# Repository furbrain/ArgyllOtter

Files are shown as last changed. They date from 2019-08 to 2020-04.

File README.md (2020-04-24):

# Shetland Attack Pony: Mobile

This is the code, construction files, pcb designs and firmware for the Shetland Attack Pony: Mobile, an 
entry to [Pi Wars 2020](https://piwars.org/).

## Why the silly name?
For the last 10 years, I have been developing a cave surveying tool called the [Shetland Attack Pony](https://github.com/furbrain/SAP5/). This uses a laser range finder, an OLED screen and a 9 axis magnetometer, accelerometer and gyro, and a PIC controller. The robot uses all of these components plus some motors and a raspberry pi, so it seemed a fitting name.

## What parts did you use?
Most of the chassis we have made ourselves with laser-cut acrylic and 3d printed parts. We have made our own pcbs with a CNC engraver/miller. 

Other components used:
* Raspberry Pi 3A
* 2200 mAh LiPo Battery (11.1V)
* [FIT0493](https://www.dfrobot.com/product-1462.html) 12V motor with encoder
* [TLE52602 motor driver](https://uk.rs-online.com/web/p/motor-driver-ics/9062978/) (x4)
* [PIC16F18877](https://www.microchip.com/wwwproducts/en/PIC16F18877) as a motor sub-controller - this allows the PI to
send a command over I2C saying "Drive forward 1m, then stop", this makes some of the autonomous challenges much easier
* [MPU9250](https://shop.pimoroni.com/products/sparkfun-imu-breakout-mpu-9250) 9 axis magnetometer, gyro and accelerometer
* [Laser range finder from aliexpress](https://www.aliexpress.com/item/4000429728611.html)

For the autonomous challenges:
* A caving helmet and light!
* A Raspberry Pi Zero Camera

For the Zombie Apocalypse Challenge:
* [Atomic power popper](https://www.amazon.co.uk/ATOMIC-POWER-POPPER-Battle-Foams/dp/B07GV3S912) - Cut this down to 
make the barrel of the cannon
* [BMP388](https://shop.pimoroni.com/products/adafruit-bmp388-precision-barometric-pressure-and-altimeter) Pressure sensor
* Another MPU9250 to measure inclination
* 12V air pump to pressurise the barrel.

## What software did you use?

We used [Freecad](https://www.freecadweb.org/) to design all the laser-cut and 3d printed parts, and  we used [gEDA](http://www.geda-project.org/) for all the PCB design.

We also used the following python libraries:
* [OpenCV](https://opencv.org/) for computer vision
* [shapely](https://pypi.org/project/Shapely/) and [pyvisgraph](https://github.com/TaipanRex/pyvisgraph) to work out an efficient route through barrels for Eco-Disaster

For the simulation code we used [pygame](http://pygame.org) for the top downview and [vtk](https://pypi.org/project/vtk/) for the 3d view

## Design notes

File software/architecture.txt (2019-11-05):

Software organisation options

Have separate functions which are called for each mode
    Pros: Simple
    Cons: Changes in controller etc need to be duplicated - violates DRY
    
Have classes for each mode which are polled at frequent intervals
    Pros: Can abstract out controller mechanism
        : Allows manager code to abort if needed
    
    Cons: More complex
          How de we handle the case where we are doing complex CV stuff and over-run
          our time slot? Maybe do the complex stuff in separate slot and poll for completion?
          
Solution:
    Total asynchronous scheme
         use asyncio
         means "main function" can keep an eye on voltage, check for home signals etc
         really quite complex

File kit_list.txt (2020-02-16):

Tools:
    Precision screwdriver kit
    Socket set
    Multimeter
    mosquito pliers
    PIC programmer
    serial connector
    crimper
    picoscope
    Glue gun
    Drill
    Calipers?

General parts:
    M3:
        40mm bolt
        20mm bolt
        nuts
        washers
        insets
        2 x 3mm spacer
        3 x 4mm bearing
        4 x 10mm hex spacer
         
    M5:
        bolt
        nuts
    jumper cables:
        male-female
        male-male
        female-female

    JST EH:
        2,4,6-way housing
        contacts
        
    Electrical tape
    
    Bungee cord
    
Controller
    
Drivetrain
    2 x Rods
    2 x springs
    1 x motor
    1 x cable
    
Grabber
    1 each of each possible part (maybe use old wooden ones)
    Servo horn adapter
    
Shooter
    1 each of support bridges (maybe use old wooden ones)
    
Laser
    1 spare unit

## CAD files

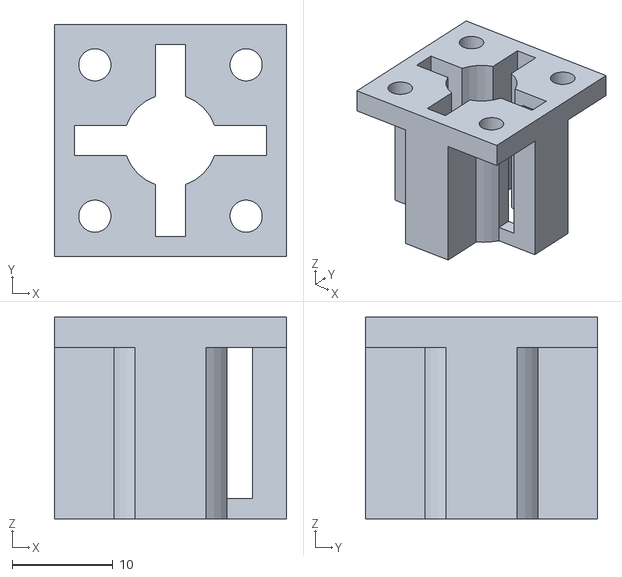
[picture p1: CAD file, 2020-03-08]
challenges/mount.stl
23.0 x 23.0 x 20.0

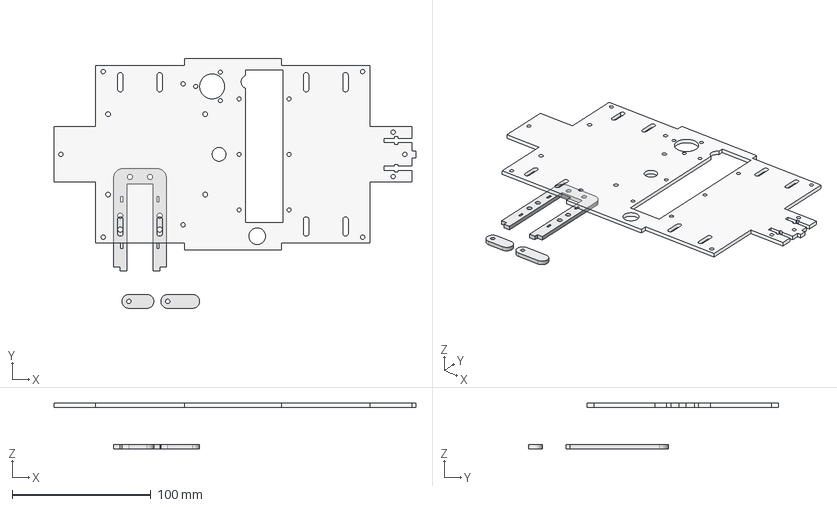
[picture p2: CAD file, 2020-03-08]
drivetrain/base.FCStd
261.0 x 180.0 x 33.0 mm
Leaf
Upper Plane
Lug1
Lug002

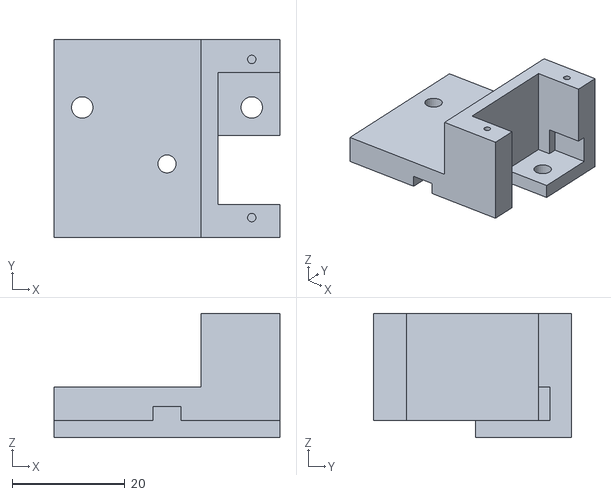
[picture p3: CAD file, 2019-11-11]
grabber/grab_mount.stl
40.0 x 35.0 x 22.0

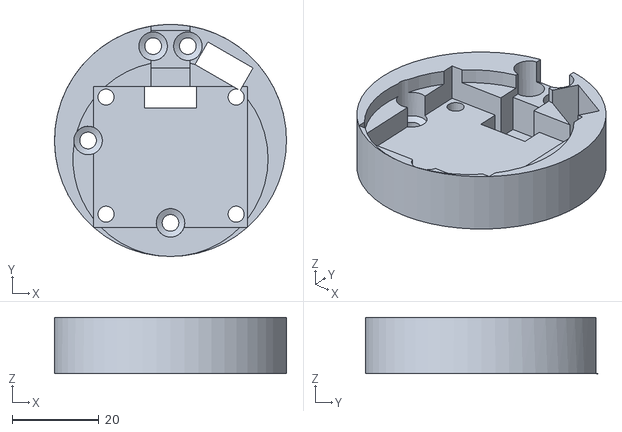
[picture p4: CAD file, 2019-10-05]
interface/headset_top.stl
53.5 x 53.5 x 13.0

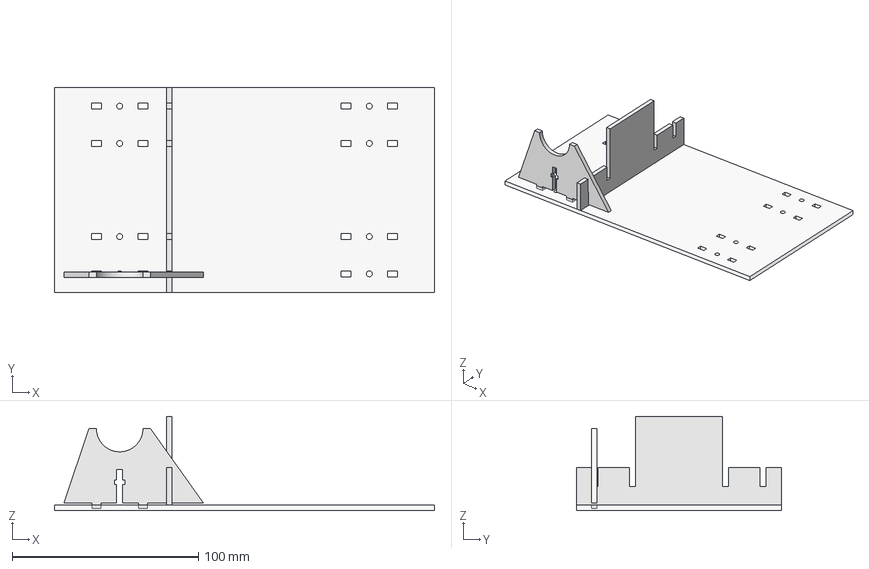
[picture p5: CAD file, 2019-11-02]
mount/mount.FCStd
204.0 x 110.0 x 50.5 mm
Stilt
Base
strut

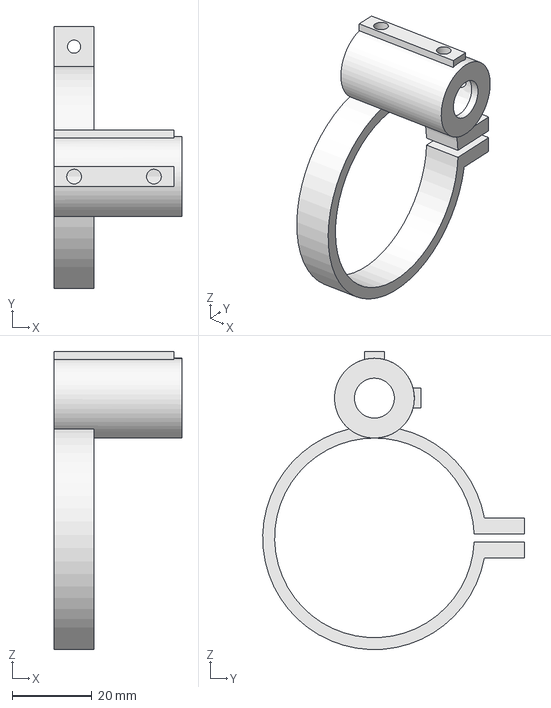
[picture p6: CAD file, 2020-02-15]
shooter/barrel_parts.FCStd
32.0 x 65.5 x 74.7 mm

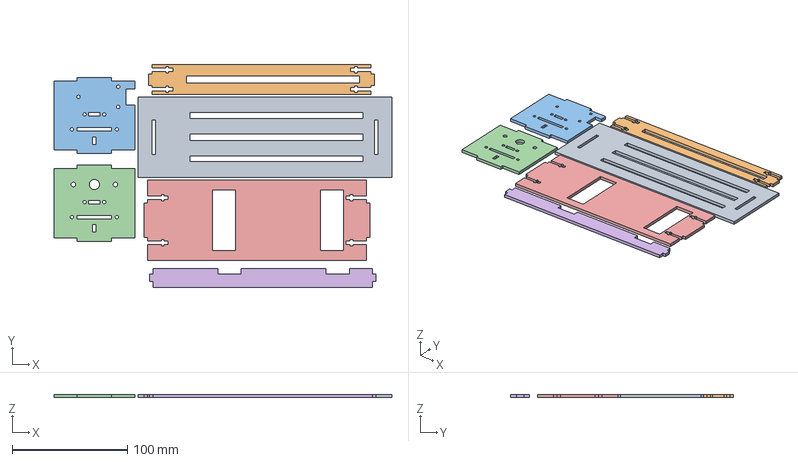
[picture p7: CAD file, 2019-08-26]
snapper/trigger/frame.FCStd
293.0 x 193.2 x 3.00 mm
Top panel
Carriage Support
Front panel
Back panel
Bottom panel
Support panel

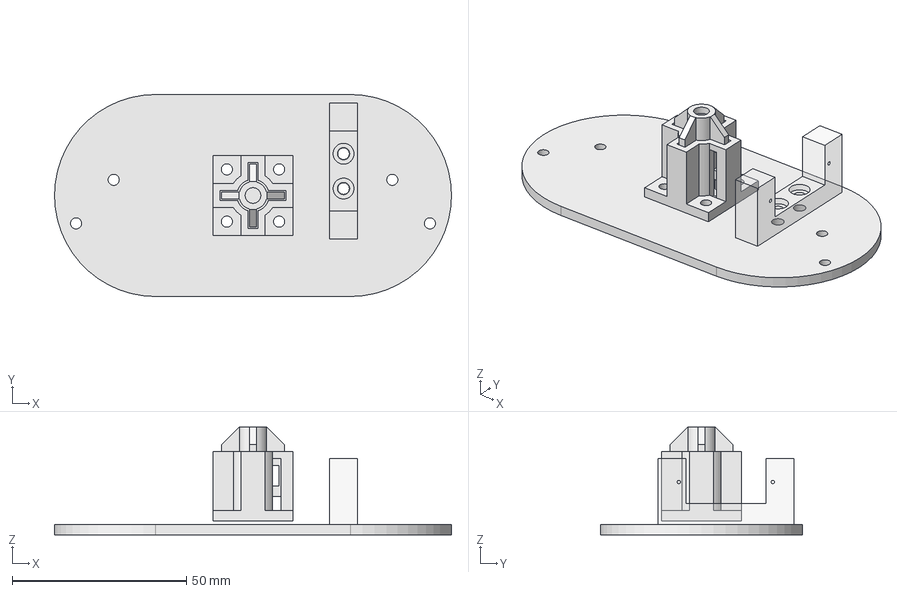
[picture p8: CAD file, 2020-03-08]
challenges/fulcrum3.FCStd
114.0 x 58.0 x 31.0 mm
slider
Mount
base
servo mount

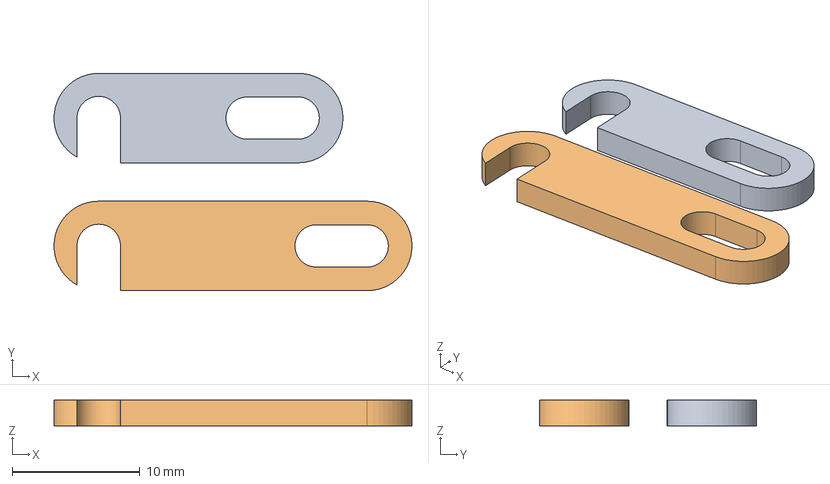
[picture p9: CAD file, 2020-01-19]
drivetrain/clips.FCStd
28.0 x 17.0 x 2.00 mm
A
B

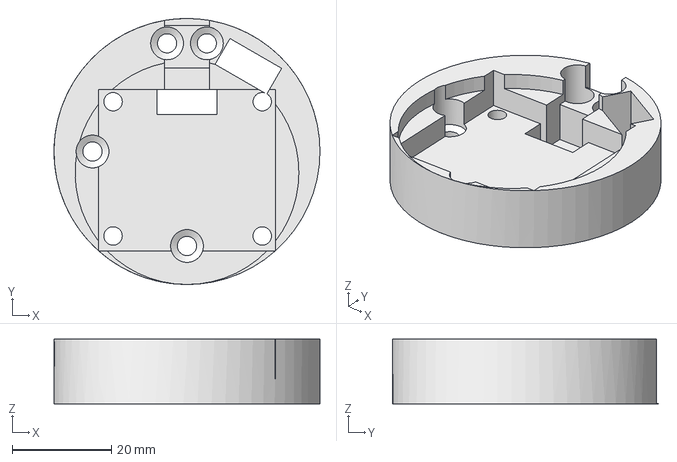
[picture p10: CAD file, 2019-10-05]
interface/headset.FCStd
53.5 x 53.5 x 13.0 mm

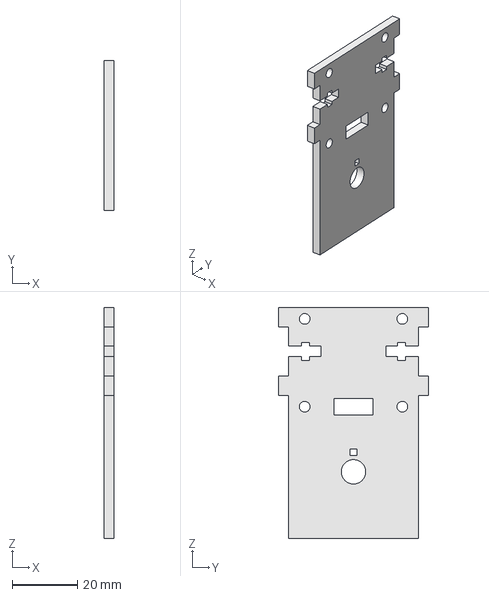
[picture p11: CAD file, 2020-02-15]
shooter/mount.FCStd
3.00 x 46.0 x 71.0 mm

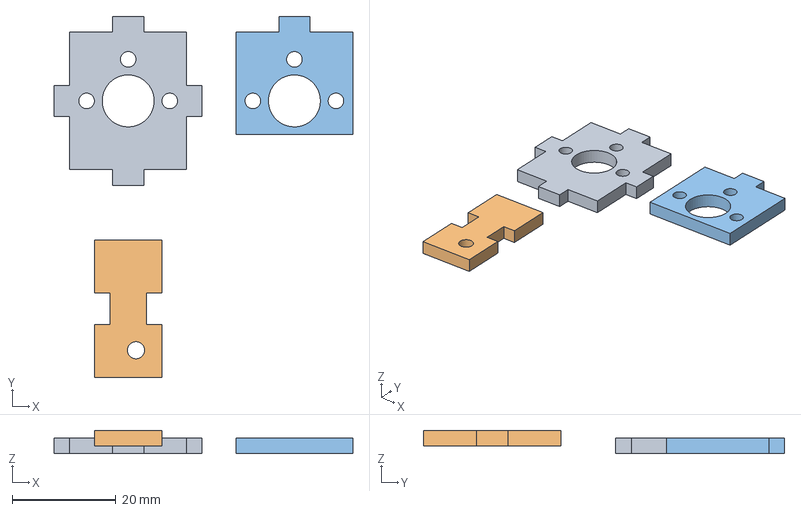
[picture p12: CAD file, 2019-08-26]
snapper/trigger/carriage.FCStd
57.5 x 69.5 x 4.50 mm
Base
SidePanel
Gap

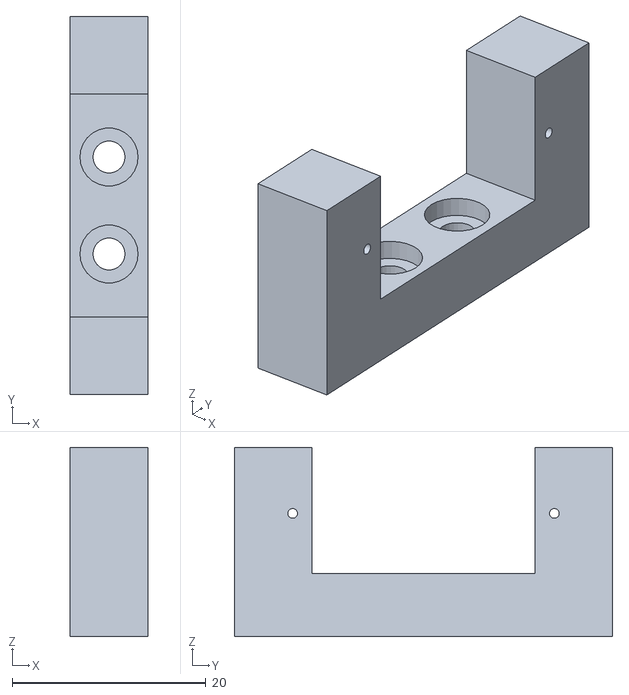
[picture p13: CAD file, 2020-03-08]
challenges/prod_mount.stl
8.00 x 39.0 x 19.5

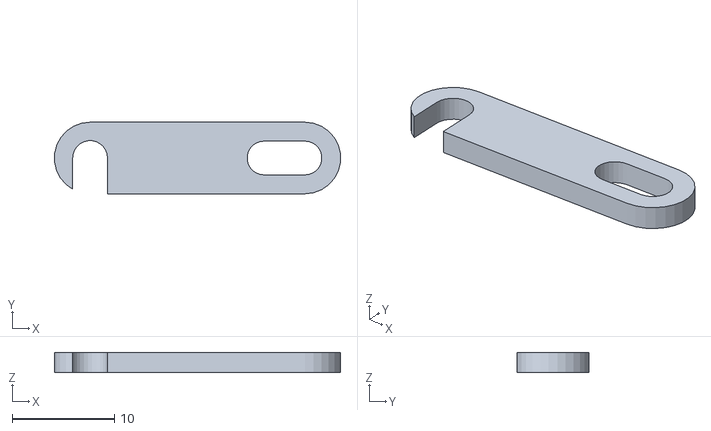
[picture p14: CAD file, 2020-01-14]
drivetrain/clip_b.stl
28.0 x 7.00 x 2.00

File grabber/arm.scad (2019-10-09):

// CSG file generated from FreeCAD 0.18.1.
group() {
 group(){
polyhedron ( points = [[-0.487106,3.465938,0.000000],[-0.487106,3.465938,3.000000],[18.978024,51.643826,0.000000],[18.978024,51.643826,3.000000],[0.487106,-3.465938,0.000000],[0.487106,-3.465938,3.000000],[24.494099,55.953453,0.000000],[24.494099,55.953453,3.000000],[1.850000,-0.000000,0.000000],[28.248360,20.624659,0.000000],[23.586061,53.798641,0.000000],[1.850000,-0.000000,3.000000],[28.248360,20.624659,3.000000],[23.586061,53.798641,3.000000],[-0.487106,3.465938,1.500000],[18.978024,51.643826,1.500000],[7.059635,5.558835,0.000000],[13.807546,9.533658,0.000000],[19.296766,15.119530,0.000000],[23.153217,21.935783,0.000000],[25.114086,29.517900,0.000000],[25.045744,37.349174,0.000000],[22.952847,44.895916,0.000000],[7.059635,5.558835,3.000000],[13.807546,9.533658,3.000000],[19.296766,15.119530,3.000000],[23.153217,21.935783,3.000000],[25.114086,29.517900,3.000000],[25.045744,37.349174,3.000000],[22.952847,44.895916,3.000000],[0.487106,-3.465938,1.500000],[-3.245143,1.311123,0.000000],[-2.758038,-2.154815,0.000000],[-3.245143,1.311123,3.000000],[-2.758038,-2.154815,3.000000],[24.494099,55.953453,1.500000],[21.248955,57.264580,0.000000],[18.490917,55.109764,0.000000],[21.248955,57.264580,3.000000],[18.490917,55.109764,3.000000],[7.992446,-1.594647,0.000000],[14.944714,1.796201,0.000000],[21.040060,6.558408,0.000000],[26.012091,12.483843,0.000000],[29.643503,19.313536,0.000000],[31.775587,26.748999,0.000000],[32.315163,34.465263,0.000000],[31.238644,42.125092,0.000000],[28.593081,49.393711,0.000000],[-0.925000,1.602147,0.000000],[-0.925000,-1.602147,0.000000],[25.473360,22.226807,0.000000],[25.473360,19.022512,0.000000],[20.811062,55.400787,0.000000],[20.811062,52.196491,0.000000],[7.992446,-1.594647,3.000000],[14.944714,1.796201,3.000000],[21.040060,6.558408,3.000000],[26.012091,12.483843,3.000000],[29.643503,19.313536,3.000000],[31.775587,26.748999,3.000000],[32.315163,34.465263,3.000000],[31.238644,42.125092,3.000000],[28.593081,49.393711,3.000000],[-0.925000,-1.602147,3.000000],[-0.925000,1.602147,3.000000],[25.473360,19.022512,3.000000],[25.473360,22.226807,3.000000],[20.811062,52.196491,3.000000],[20.811062,55.400787,3.000000],[1.850000,-0.000000,1.500000],[28.248360,20.624659,1.500000],[23.586061,53.798641,1.500000],[21.326979,48.159222,0.160588],[24.953423,37.960323,0.160588],[24.724274,27.138304,0.160588],[20.669365,17.102055,0.160588],[13.316594,9.158165,0.160588],[3.623200,4.340831,0.160588],[25.330978,32.538895,0.160588],[23.603994,43.224686,0.160588],[17.354227,12.795743,0.160588],[8.688965,6.308692,0.160588],[23.153217,21.935783,0.160588],[-2.693777,2.234628,0.758522],[-1.973478,-2.890568,0.758522],[-3.465938,-0.487106,0.758522],[22.324417,57.248833,0.758522],[18.246017,54.062439,0.758522],[19.581245,56.556679,0.758522],[30.102057,44.484524,0.000000],[6.751485,4.040147,0.000000],[2.859724,-2.700582,0.000000],[26.210295,51.225250,0.000000],[14.535009,4.040147,0.000000],[18.426771,10.780876,0.000000],[22.318533,17.521606,0.000000],[26.210295,24.262335,0.000000],[30.102057,31.003063,0.000000],[26.210295,37.743793,0.000000],[30.102057,44.484524,3.000000],[6.751485,4.040147,3.000000],[2.859724,-2.700582,3.000000],[26.210295,51.225250,3.000000],[14.535009,4.040147,3.000000],[18.426771,10.780876,3.000000],[22.318533,17.521606,3.000000],[26.210295,24.262335,3.000000],[30.102057,31.003063,3.000000],[26.210295,37.743793,3.000000],[0.138191,1.844831,0.668289],[0.138191,-1.844831,0.668289],[-1.850000,-0.000000,0.668289],[26.536551,22.469490,0.668289],[26.536551,18.779827,0.668289],[24.548361,20.624659,0.668289],[21.874252,55.643471,0.668289],[21.874252,51.953808,0.668289],[19.886061,53.798641,0.668289]], triangles = [[73,15,2],[22,73,2],[15,73,3],[20,79,21],[75,27,20],[19,75,20],[28,29,80],[74,21,28],[21,79,28],[79,20,27],[28,79,27],[80,74,28],[73,22,29],[3,73,29],[80,29,22],[80,22,21],[21,74,80],[81,25,18],[17,81,18],[77,24,17],[26,76,25],[25,81,24],[17,24,81],[76,18,25],[78,0,14],[14,1,78],[23,78,1],[24,77,82],[82,16,23],[82,23,24],[17,16,82],[82,77,17],[78,23,16],[0,78,16],[75,83,26],[26,27,75],[83,76,26],[76,83,19],[19,18,76],[83,75,19],[32,4,85],[30,34,85],[85,34,32],[34,30,5],[4,30,85],[14,0,84],[34,33,86],[14,33,1],[33,14,84],[86,33,31],[0,31,84],[86,32,34],[31,32,86],[84,31,33],[37,2,88],[15,39,88],[88,39,37],[39,15,3],[2,15,88],[39,38,89],[87,35,6],[35,38,7],[38,35,87],[89,38,36],[6,36,87],[89,37,39],[36,37,89],[87,36,38],[2,54,22],[10,53,6],[93,22,54],[2,37,54],[93,54,10],[90,99,22],[93,48,22],[47,90,48],[90,22,48],[48,93,6],[93,10,6],[53,36,6],[53,54,37],[37,36,53],[92,8,40],[94,41,91],[4,92,40],[91,40,8],[0,8,49],[92,4,8],[0,91,8],[0,49,31],[32,50,4],[50,8,4],[49,50,31],[32,31,50],[40,91,41],[18,43,95],[41,94,42],[96,52,43],[42,95,43],[19,96,18],[96,43,18],[91,0,16],[18,95,17],[91,16,94],[95,42,94],[95,94,17],[94,16,17],[44,9,45],[43,52,44],[98,45,20],[97,19,20],[97,20,45],[99,98,21],[22,99,21],[20,21,98],[46,99,47],[99,90,47],[45,98,46],[98,99,46],[97,45,9],[51,52,19],[96,19,52],[9,44,52],[51,97,9],[97,51,19],[3,29,68],[13,7,69],[103,68,29],[3,68,39],[103,13,68],[100,29,109],[103,29,63],[62,63,100],[100,63,29],[63,7,103],[103,7,13],[69,7,38],[69,39,68],[39,69,38],[102,55,11],[104,101,56],[5,55,102],[101,11,55],[1,65,11],[102,11,5],[1,11,101],[1,33,65],[34,5,64],[64,5,11],[65,33,64],[34,64,33],[55,56,101],[25,105,58],[56,57,104],[106,58,66],[57,58,105],[26,25,106],[106,25,58],[101,23,1],[25,24,105],[101,104,23],[105,104,57],[105,24,104],[104,24,23],[59,60,12],[58,59,66],[108,27,60],[107,27,26],[107,60,27],[109,28,108],[29,28,109],[27,108,28],[61,62,109],[109,62,100],[60,61,108],[108,61,109],[107,12,60],[67,26,66],[106,66,26],[12,66,59],[67,12,107],[107,26,67],[48,35,63],[48,6,35],[63,35,7],[46,60,45],[44,45,60],[47,61,46],[60,46,61],[61,47,62],[63,47,48],[47,63,62],[43,44,58],[42,58,57],[56,42,57],[58,42,43],[41,55,40],[30,55,5],[30,40,55],[4,40,30],[55,41,56],[42,56,41],[58,44,59],[44,60,59],[50,111,8],[70,111,64],[111,50,64],[64,11,70],[8,111,70],[70,110,8],[64,112,65],[70,11,65],[65,110,70],[112,49,65],[8,110,49],[112,64,50],[49,112,50],[110,65,49],[52,114,9],[71,114,66],[114,52,66],[66,12,71],[9,114,71],[71,113,9],[66,115,67],[71,12,67],[67,113,71],[115,51,67],[9,113,51],[115,66,52],[51,115,52],[113,67,51],[54,117,10],[72,117,68],[117,54,68],[68,13,72],[10,117,72],[72,116,10],[68,118,69],[72,13,69],[69,116,72],[118,53,69],[10,116,53],[118,68,54],[53,118,54],[116,69,53]]);
}
}

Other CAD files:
grabber/mount.FCStd
grabber/arm.FCStd
interface/encoder_adapter.FCStd
shooter/sight2.stl
challenges/Barrel1.stl
challenges/card_holder.FCStd
challenges/card_holder.stl
challenges/fulcrum2.FCStd
challenges/prodder.stl
challenges/prodder2.stl
challenges/slider.stl
drivetrain/Spring mount.FCStd
drivetrain/clip_a.stl
drivetrain/clips.stl
drivetrain/hub.FCStd
drivetrain/hub.stl
drivetrain/laser holder.FCStd
drivetrain/laser_holder.stl
drivetrain/mounts.stl
drivetrain/pcb mounts.FCStd
drivetrain/spring_mount.stl
drivetrain/suspension_lug.FCStd
drivetrain/suspension_lug.stl
grabber/arm.stl
grabber/grab_servo.stl
interface/encoder_adapter.stl
interface/front_panel.FCStd
interface/front_panel.stl
interface/headset.stl
interface/knob.FCStd
interface/knob.stl
shooter/end_cap.stl
shooter/pivoteer.stl
shooter/ring.stl
shooter/servo_adapter.stl
shooter/sight.stl
snapper/trigger/carriage.dxf
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

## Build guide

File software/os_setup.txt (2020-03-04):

System set up notes:
Needs approxeng.input as per lorraine's blog
Need to install servoblaster, this needs to be set as PCM to avoid interfering
with neopixels.
Set to 1us output resolution, set output 0 only
Need to install jgarffs neopixel python lib - which needs to be installed from source as seems to be using an old version of main lib
Install simple-pid python thingy - needs to be installed from github as not on raspbian currently (not currently used...)
Need opencv, imutils, shapely, pyvisgraph, tqdm, sharedarray from pip3
sudo apt install libgeos-dev

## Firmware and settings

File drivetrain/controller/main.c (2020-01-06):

/**
  Generated Main Source File

  Company:
    Microchip Technology Inc.

  File Name:
    main.c

  Summary:
    This is the main file generated using PIC10 / PIC12 / PIC16 / PIC18 MCUs

  Description:
    This header file provides implementations for driver APIs for all modules selected in the GUI.
    Generation Information :
        Product Revision  :  PIC10 / PIC12 / PIC16 / PIC18 MCUs - 1.77
        Device            :  PIC16F18877
        Driver Version    :  2.00
*/

/*
    (c) 2018 Microchip Technology Inc. and its subsidiaries. 
    
    Subject to your compliance with these terms, you may use Microchip software and any 
    derivatives exclusively with Microchip products. It is your responsibility to comply with third party 
    license terms applicable to your use of third party software (including open source software) that 
    may accompany Microchip software.
    
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
    IN NO EVENT WILL MICROCHIP BE LIABLE FOR ANY INDIRECT, SPECIAL, PUNITIVE, 
    INCIDENTAL OR CONSEQUENTIAL LOSS, DAMAGE, COST OR EXPENSE OF ANY KIND 
    WHATSOEVER RELATED TO THE SOFTWARE, HOWEVER CAUSED, EVEN IF MICROCHIP 
    HAS BEEN ADVISED OF THE POSSIBILITY OR THE DAMAGES ARE FORESEEABLE. TO 
    THE FULLEST EXTENT ALLOWED BY LAW, MICROCHIP'S TOTAL LIABILITY ON ALL 
    CLAIMS IN ANY WAY RELATED TO THIS SOFTWARE WILL NOT EXCEED THE AMOUNT 
    OF FEES, IF ANY, THAT YOU HAVE PAID DIRECTLY TO MICROCHIP FOR THIS 
    SOFTWARE.
*/
#pragma warning disable 520
#include "mcc_generated_files/mcc.h"

/*
                         Main application
 */
#include <stdint.h>
#include <stdbool.h>
#include <string.h>
#include <stdlib.h>
#include "comms.h"
#include "pid.h"
#include "wheels.h"

const uint8_t ADC_CHANNELS[] = {
    FRONT_GROUND, 
    FL_CURRENT, 
    FR_CURRENT,
    REAR_GROUND,
    RL_CURRENT,
    RR_CURRENT, 
    BATT_VOLTAGE,
    channel_DAC1
};

volatile bool tick = false;
volatile command_t cmd;

inline void ADCC_SetChannel(uint8_t channel) {
    ADPCH = channel;
}


void OneHundredHertz(void) {
    tick = true;
}

#define within(a, b, delta) (abs(a-b) < delta)

void set_wheel_differentials(int32_t left, int32_t right, int16_t speed) {
    int32_t left_speed, right_speed;
    if (left == right) {
        left_speed = right_speed = speed;
    } else {
        int32_t max_distance = max(abs(left), abs(right));
        left_speed = abs((left * speed) / max_distance);
        right_speed = abs((right * speed) / max_distance);
    }
    wheel_move_to(&wheels[FRONT_LEFT], left_speed);
    wheel_move_to(&wheels[REAR_LEFT], left_speed);
    wheel_move_to(&wheels[FRONT_RIGHT], right_speed);
    wheel_move_to(&wheels[REAR_RIGHT], right_speed);    
}

void Update(void) {
    static uint8_t count = 0;
    wheel_t* whl;
    count++;
    if (count >= SAMPLE_SKIP) {
        FOR_ALL_WHEELS(whl) {
            wheel_update_velocity(whl);
        }
    }
    if (new_command) {
        cmd = *command;
        raise_alert(ALERT_NOALERT);
        FOR_ALL_WHEELS(whl) {
            whl->stopped=false;
        }
        if (cmd.flags & FLAG_RESET_POS) {
                wheels_reset_position();            
        }
        if (cmd.flags & FLAG_SOFT_START) {
            FOR_ALL_WHEELS(whl) {
                wheel_soft_start(whl);
            }
        }
        switch (cmd.mode) {
            case CMD_STOP:
                FOR_ALL_WHEELS(whl) {
                    wheel_stop(whl);
                }
                break;
            case CMD_DRIVE:
                wheel_set_speed(&wheels[FRONT_LEFT], cmd.left_speed);
                wheel_set_speed(&wheels[REAR_LEFT], cmd.left_speed);
                wheel_set_speed(&wheels[FRONT_RIGHT], cmd.right_speed);
                wheel_set_speed(&wheels[REAR_RIGHT], cmd.right_speed);                
                break;
            case CMD_INDIVIDUAL:
                for(uint8_t i = 0; i< 4; i++) {
                    wheel_set_power(&wheels[i], cmd.motor_speed[i]);
                }
                break;
            case CMD_FAST_DISTANCE:
            case CMD_DISTANCE:
                wheel_set_target_pos(&wheels[FRONT_LEFT], cmd.left_distance);
                wheel_set_target_pos(&wheels[REAR_LEFT], cmd.left_distance);
                wheel_set_target_pos(&wheels[FRONT_RIGHT], cmd.right_distance);
                wheel_set_target_pos(&wheels[REAR_RIGHT], cmd.right_distance);
                set_wheel_differentials(cmd.left_distance, cmd.right_distance, cmd.max_speed);
                break;
        }
        new_command = false;
    }
    if (cmd.mode == CMD_DISTANCE) {
        /* left */
        bool nearby = false;
        bool stopped = false;
        
        FOR_ALL_WHEELS(whl) {
            if (whl->stopped) {
                stopped = true;
                break;
            }
            if (within(whl->target_pos, *whl->pos, 10)) {
                raise_alert(ALERT_DESTINATION);
                stopped = true;
                break;
            } else if (within(whl->target_pos, *whl->pos, 300)){
                nearby = true;
            }
        }
        if (stopped) {
            FOR_ALL_WHEELS(whl) {
                wheel_stop(whl);
                cmd.mode = CMD_STOP;
            }
        } else if (nearby) {
            set_wheel_differentials(cmd.left_distance, cmd.right_distance, cmd.max_speed/4);
        } else {
            set_wheel_differentials(cmd.left_distance, cmd.right_distance, cmd.max_speed);
        }
    } else if (cmd.mode == CMD_FAST_DISTANCE) {
        FOR_ALL_WHEELS(whl) {
            if (!*alert_status) {
                if (abs(*whl->pos) > abs(whl->target_pos)) {
                    raise_alert(ALERT_DESTINATION);
                    break;
                } 
            }
        }
    }
    if (count >= SAMPLE_SKIP) {
        count = 0;
        FOR_ALL_WHEELS(whl) {
            if (cmd.mode != CMD_INDIVIDUAL) {
                wheel_update_power(whl);
            }
        }
        FOR_ALL_WHEELS(whl) {
            //wheel_check_current(whl);
        }
    }
}

void ADCResultReady(void) {
    static uint8_t channel_index = 0;
    static uint16_t ground = 0;
    uint8_t channel = ADC_CHANNELS[channel_index];
    uint16_t result = ADCC_GetConversionResult();
    switch (channel) {
        case FRONT_GROUND:
        case REAR_GROUND:
            ground = result;
            break;            
        case FL_CURRENT:
            current[FRONT_LEFT] = (result - ground) * 50;
            break;
        case FR_CURRENT:
            current[FRONT_RIGHT] = (result - ground) * 50;
            break;
        case RL_CURRENT:
            current[REAR_LEFT] = (result - ground) * 50;
            break;           
        case RR_CURRENT:
            current[REAR_RIGHT] = (result - ground) * 50;
            break;
        case BATT_VOLTAGE:
            *batt_voltage = result * 11 * 2;
            break;
        case channel_DAC1:
            *peripheral_voltage = result * 4 * 2;
            break;
        default:
            break;
    }
    channel_index = (channel_index+1) % sizeof(ADC_CHANNELS);
    channel = ADC_CHANNELS[channel_index];
    ADCC_SetChannel(channel);
}


void main(void)
{
    wheel_t* whl;
    SYSTEM_Initialize();
    comms_init();
    wheels_init();
    FOR_ALL_WHEELS(whl) {
        wheel_stop(whl);
    }
    TMR6_SetInterruptHandler(OneHundredHertz);
    TMR1_StartTimer();
    ADCC_SetADIInterruptHandler(ADCResultReady);
    ADCC_SetChannel(FRONT_GROUND);
    // Enable the Interrupts
    INTERRUPT_GlobalInterruptEnable();
    INTERRUPT_PeripheralInterruptEnable();
    while (1)
    {
        while (!tick) {
            NOP();
        }
        tick = false;
        Update();
    }
}
/**
 End of File
*/

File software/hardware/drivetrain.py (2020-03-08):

#!/usr/bin/env python3
import asyncio
import logging
import math
import struct
import time

# noinspection PyUnresolvedReferences
import gpiozero
import numpy as np
# noinspection PyUnresolvedReferences
import smbus

import settings
from util import logged
from . import orientation

I2C_ADDRESS = 0x33
ALERT_REGISTER = 0x5F
RESET_POSITION = 0x01
SOFT_START = 0x02

DRIVE_CAL_FILE = "/home/pi/drivetrain.npz"


class DriveError(Exception):
    pass


# noinspection PyAttributeOutsideInit,PyAttributeOutsideInit,PyAttributeOutsideInit
class DriveCalibration(settings.Settings):
    def default(self):
        self.spin_k = 0
        self.forward_k = 0
        self.reverse_k = 0


class Drive:
    def __init__(self, bus=None, wheel_diameter=70.0, clicks_per_revolution=374):
        if bus is None:
            self.bus = smbus.SMBus(1)
        else:
            self.bus = bus
        self.cal = DriveCalibration()
        self.clicks_per_mm = clicks_per_revolution / (math.pi * wheel_diameter)
        self.orientation = orientation.Orientation(bus=self.bus)
        self.alert = gpiozero.Button(4)
        self.orientation.calibrate_gyro()
        self.stop(reset_position=True)

    def __str__(self):
        return "Drive instance"

    @staticmethod
    def get_flags(soft_start, reset_position):
        flags = 0
        if soft_start:
            flags |= SOFT_START
        if reset_position:
            flags |= RESET_POSITION
        return flags

    def reset_alert(self):
        self.get_alert()
        self.bus.write_i2c_block_data(I2C_ADDRESS, ALERT_REGISTER, [0])

    def get_alert(self):
        return self.bus.read_i2c_block_data(I2C_ADDRESS, ALERT_REGISTER, 1)[0]

    def mm2c(self, *args):
        return [int(x * self.clicks_per_mm) for x in args]

    def c2mm(self, *args):
        return [int(x / self.clicks_per_mm) for x in args]

    @logged
    def stop(self, reset_position=False):
        flags = self.get_flags(soft_start=False, reset_position=reset_position)
        self.bus.write_i2c_block_data(I2C_ADDRESS, 0x0, [0, flags])

    @logged
    def drive(self, left, right=None, soft_start=False, reset_position=False):
        if right is None:
            right = left
        flags = self.get_flags(soft_start, reset_position)
        args = self.mm2c(left, right) + [soft_start]
        command = struct.pack("<BBhhB", 1, flags, *args)
        self.bus.write_i2c_block_data(I2C_ADDRESS, 0x0, list(command))

    @logged
    def goto(self, max_speed, right, left=None, fast=False, soft_start=False, reset_position=True):
        flags = self.get_flags(soft_start, reset_position)
        if fast:
            cmd = 5
        else:
            cmd = 2
        if left is None:
            left = right
        args = self.mm2c(left, right, max_speed)
        # noinspection SpellCheckingInspection
        command = struct.pack("<BBiih", cmd, flags, *args)
        self.bus.write_i2c_block_data(I2C_ADDRESS, 0x0, list(command))

    @logged
    def set_powers(self, fr, fl, rr, rl, soft_start=False, reset_position=False):
        args = fr, fl, rr, rl
        flags = self.get_flags(soft_start, reset_position)
        # noinspection SpellCheckingInspection
        command = struct.pack("<BBhhhh", 4, flags, *args)
        self.bus.write_i2c_block_data(I2C_ADDRESS, 0x0, list(command))

    @logged
    def get_positions(self):
        for i in range(5):
            data = self.bus.read_i2c_block_data(I2C_ADDRESS, 0x10, 0x10)
            positions = struct.unpack("4i", bytes(data))
            if any(abs(x) > 10000 for x in positions):
                print("bad position, trying again")
                time.sleep(0.02)
                continue
            return self.c2mm(*positions)
        # noinspection PyUnboundLocalVariable
        raise DriveError(
            "Couldn't get reasonable positions, latest readings are" + ', '.join(str(x) for x in positions))

    @logged
    async def a_goto(self, max_speed, right, left=None, fast=False, soft_start=False, reset_position=True,
                     accurate=False):
        self.goto(max_speed, right, left, fast, soft_start, reset_position)
        while True:
            await asyncio.sleep(0.01)
            if not self.alert.is_pressed:
                await asyncio.sleep(0.01)
                if accurate:
                    await asyncio.sleep(0.1)
                return np.mean(self.get_positions())

    @logged
    def get_velocities(self):
        data = self.bus.read_i2c_block_data(I2C_ADDRESS, 0x20, 0x08)
        velocities = struct.unpack("4h", bytes(data))
        return self.c2mm(*velocities)

    @logged
    def get_constants(self):
        data = self.bus.read_i2c_block_data(I2C_ADDRESS, 0x30, 0x10)
        p, i, d, ratio = struct.unpack("4f", bytes(data))
        return {'kP': p, 'kI': i, 'kD': d, 'ratio': ratio}

    @logged
    def get_powers(self):
        powers = [0, 0, 0, 0]
        for i in range(5):
            data = self.bus.read_i2c_block_data(I2C_ADDRESS, 0x20, 0x10)
            powers = struct.unpack("<8h", bytes(data))[4:]
            if any(abs(x) > 1024 for x in powers):
                time.sleep(0.01)
                continue
            return powers
        raise DriveError("Couldn't get reasonable powers, latest readings are" + ', '.join(str(x) for x in powers))

    @logged
    def get_currents(self):
        data = self.bus.read_i2c_block_data(I2C_ADDRESS, 0x40, 0x08)
        currents = struct.unpack("4h", bytes(data))
        return [x / 1000 for x in currents]

    @logged
    def get_voltages(self):
        data = self.bus.read_i2c_block_data(I2C_ADDRESS, 0x50, 0x08)
        peripheral, _, main, _ = struct.unpack("4h", bytes(data))
        peripheral /= 1000.0
        main /= 1000.0
        return peripheral, main
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

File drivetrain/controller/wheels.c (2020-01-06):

#include "wheels.h"
#include "comms.h"
#include "mcc_generated_files/pin_manager.h"
#include "mcc_generated_files/adcc.h"
#include "mcc_generated_files/pwm1.h"
#include "mcc_generated_files/pwm2.h"
#include "mcc_generated_files/pwm4.h"
#include "mcc_generated_files/pwm5.h"
#include "mcc_generated_files/interrupt_manager.h"
#include "mcc_generated_files/tmr1.h"

#define update_times(wheel)\
    last_times[wheel] = times[wheel];\
    times[wheel] = TMR1_ReadTimer();    

uint16_t times[4] = {0};
uint16_t last_times[4] = {0};


int16_t power2duty(float power) {
    return (int16_t)(power*0x3ff);
}

float duty2power(int16_t duty) {
    return (float)(duty / 1023.0);
}

void FR_set_direction(uint8_t dir) {
    FR_DIRECTION_LAT = dir;
}

void FL_set_direction(uint8_t dir) {
    FL_DIRECTION_LAT = dir;
}

void RR_set_direction(uint8_t dir) {
    RR_DIRECTION_LAT = dir;
}

void RL_set_direction(uint8_t dir) {
    RL_DIRECTION_LAT = dir;
}

void FR_sensor(void) {
    if (!FR_SENSE2_GetValue()) {
        position[FRONT_RIGHT]++;
    } else {
        position[FRONT_RIGHT]--;
    }
    update_times(FRONT_RIGHT);
}

void FL_sensor(void) {
    if (!FL_SENSE2_GetValue()) {
        position[FRONT_LEFT]++;
    } else {
        position[FRONT_LEFT]--;
    }
    update_times(FRONT_LEFT);
}

void RR_sensor(void) {
    if (!RR_SENSE2_GetValue()) {
        position[REAR_RIGHT]++;
    } else {
        position[REAR_RIGHT]--;
    }
    update_times(REAR_RIGHT);
}

void RL_sensor(void) {
    if (!RL_SENSE2_GetValue()) {
        position[REAR_LEFT]++;
    } else {
        position[REAR_LEFT]--;
    }
    update_times(REAR_LEFT);
}


pid_t pids[4] = {0};

#define WHEEL_DATA(initials, name) \
    {\
        initials##_CURRENT,\
        false,\
        0,\
        &position[name],\
        0,\
        &current[name],\
        0,\
        1 << 4 + name,\
        name\
    }

wheel_t wheels[4] = {
    WHEEL_DATA(FR, FRONT_RIGHT),
    WHEEL_DATA(FL, FRONT_LEFT),
    WHEEL_DATA(RR, REAR_RIGHT),
    WHEEL_DATA(RL, REAR_LEFT),
};



void (*set_direction[4])(uint8_t) = {
    FR_set_direction,
    FL_set_direction,
    RR_set_direction,
    RL_set_direction
};

void (*set_pwm[4])(uint16_t) = {
    PWM5_LoadDutyValue,
    PWM1_LoadDutyValue,
    PWM2_LoadDutyValue,
    PWM4_LoadDutyValue
};


void wheels_init(void) {
    wheel_t* whl;
    uint8_t idx;
    IOCAF3_SetInterruptHandler(FL_sensor);
    IOCAF2_SetInterruptHandler(FR_sensor);
    IOCCF5_SetInterruptHandler(RL_sensor);
    IOCBF5_SetInterruptHandler(RR_sensor);
    FOR_ALL_WHEELS(whl) {
        idx = whl->index;
        pid_init(&pids[idx], 0, 0);
        pids[idx].pOnE=true;
        pid_setPoint(&pids[idx], 0);
    }
}

void wheels_reset_position(void) {
    wheel_t *whl;
    FOR_ALL_WHEELS(whl) {
        *whl->pos = 0;
        whl->last_pos = 0;
    }  
}

void wheel_set_power(wheel_t *whl, int16_t duty) {
    uint8_t idx = whl->index;
    if (duty < 0) {
        set_direction[idx](WHEEL_REVERSE);
    } else {
        set_direction[idx](WHEEL_FORWARD);
    }    
    set_pwm[idx]((uint16_t)duty);
    power[idx] = duty;
}

void wheel_set_speed(wheel_t *whl, float speed) {
    pid_setPoint(&pids[whl->index], speed);
}    

void wheel_set_target_pos(wheel_t *whl, int32_t target) {
    whl->target_pos = target;
}    

void wheel_soft_start(wheel_t *whl) {
    uint8_t idx = whl->index;
    pid_init(&pids[idx], (float)velocity[idx], duty2power(power[idx]));
}

void wheel_update_power(wheel_t *whl) {
    float output;
    int16_t duty;
    uint8_t idx = whl->index;
    if (whl->stopped) return;
    output = pid_compute(&pids[idx], (float)velocity[idx]);
    duty = power2duty(output);
    wheel_set_power(whl, duty);
}

void wheel_update_velocity(wheel_t *whl) {
    int32_t diff = *whl->pos - whl->last_pos;
    int32_t speed;
    uint8_t idx = whl->index;
    if (diff==0) {
        velocity[idx] = 0;
    } else if ((-30 < diff) && (diff < 30)) {
        uint16_t dt = times[idx] - last_times[idx];        
        if (dt==0) {
            velocity[idx] = diff * SAMPLE_FREQUENCY/SAMPLE_SKIP;
        } else {
            speed = 1000000/dt;
            if (diff<0) {
                velocity[idx] = -speed;
            } else {
                velocity[idx] = speed;
            }
        }
    } else {
        velocity[idx] = diff * SAMPLE_FREQUENCY/SAMPLE_SKIP;
    }
    whl->last_pos = *whl->pos;
}

void wheel_stop(wheel_t *whl) {
    uint8_t idx = whl->index;
    set_direction[idx](0);
    set_pwm[idx](0);
    whl->stopped = true;
    pid_init(&pids[idx], 0, 0);
}

void wheel_move_to(wheel_t *whl, int16_t max_speed) {
    if (*whl->pos < whl->target_pos) {
        wheel_set_speed(whl, max_speed);
    } else {
        wheel_set_speed(whl, -max_speed);
    }
}
void wheel_check_current(wheel_t *whl) {
    wheel_t *whl2;
    volatile int16_t local_current;
    volatile int16_t local_current_limit;
    
    INTERRUPT_GlobalInterruptDisable();
    local_current = *whl->current;
    local_current_limit = *current_limit;
    INTERRUPT_GlobalInterruptEnable();
    
    if (local_current > local_current_limit) {
        whl->over_current_count++;
        if (whl->over_current_count > 10) {
            FOR_ALL_WHEELS(whl2) {
                wheel_stop(whl2);
            }
            raise_alert(ALERT_OVERCURRENT | whl->bitmask);
        }
    } else {
        whl->over_current_count = 0;
    }
}

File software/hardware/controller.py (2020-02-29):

import asyncio

from approxeng.input.selectbinder import ControllerResource

from modes import messages
from util import start_task


class Controller:
    def __init__(self, event_queue):
        self.event_queue = event_queue
        start_task(self.monitor())

    def add_event(self, msg):
        self.event_queue.put(msg)

    def button_handler(self, button):
        self.add_event(messages.ControllerButtonMessage(button.sname))

    async def monitor(self, poll_time=0.1):
        while True:
            try:
                controller = ControllerResource(dead_zone=0.05, hot_zone=0.1)
            except IOError:
                # no joystick found, wait a bit and try again
                await asyncio.sleep(1.0)
            else:
                with controller as joystick:
                    joystick.buttons.register_button_handler(self.button_handler,
                                                             list(joystick.buttons.buttons.keys()))

                    self.add_event(messages.ControllerConnectedMessage(True, joystick))
                    while joystick.connected:
                        await asyncio.sleep(poll_time)
                self.add_event(messages.ControllerConnectedMessage(False))

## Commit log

2019-05-04 Add Mk1 launcher
    [carriage.FCStd, frame.FCStd, globals.FCStd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]
2019-08-26 Various tweaks
    [carriage.FCStd, frame.FCStd, trigger.dxf]
2019-08-26 Add drivetrain folder and first draft
    [base.FCStd]
2019-08-26 Start developing motor controller
    [motorboard.sch]
2019-08-26 update dxfs
    [carriage.dxf, frame.dxf]
2019-08-31 Update chassis base
    [base.FCStd]
2019-08-31 Add symbols and footprints for motor driver
    [motorboard.sch]
2019-08-31 Redesign controller and driver boards
    [controller.sch, motorboard.sch]
2019-09-03 Further mods, add hub designs
    [base.FCStd, hub.FCStd]
2019-09-03 Various bug fixes
    [controller.sch, hub.stl, power.sch]
2019-09-04 Work on upper plane
    [base.FCStd]
2019-09-04 More work on controller board
    [controller.sch]
2019-09-04 Upper layer and suspension holes
    [base.FCStd]
2019-09-04 Create washer for suspension
    [Spring mount.FCStd]
2019-09-04 PCB mounts
    [pcb mounts.FCStd]
2019-09-04 Bug fixes
    [Spring mount.FCStd, base.FCStd]
2019-09-08 Get Motor Controller pins and modules setup
2019-09-08 Add pid and i2c code
2019-09-08 Various fixes for controller pcb
    [controller.sch, power.sch]
2019-09-08 Hub repairs
    [hub.FCStd, hub.stl]
2019-09-29 Update base layer to allow mounting of RPi and hole for battery etc
    [base.FCStd]
2019-09-29 Get voltage and current measurement working
2019-09-29 Add extra grub screw
    [hub.FCStd, hub.stl]
2019-09-29 Add knob design
    [knob.FCStd]
2019-09-29 Add stl files
    [knob.stl, mounts.stl, spring_mount.stl]
2019-09-29 Create interface dir
    [knob.FCStd, knob.stl]
2019-09-29 Create front panel
    [front_panel.FCStd, front_panel.stl]
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2019-09-29 encoder and manual drive
2019-10-01 Start work on headset parts
    [encoder_adapter.FCStd, encoder_adapter.stl, encoder_mount.FCStd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]
2019-10-02 Rename files
    [headset.FCStd, headset.stl]
2019-10-02 Further work...
    [headset.FCStd, headset_top.stl]
2019-10-05 More work on headset
    [headset.FCStd, headset_top.stl]
2019-10-09 Create adapter board
    [drive.sch, headset.sch, peripheral.sch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]
2019-10-09 Further mods to grabber mechanism
    [arm.FCStd, arm.scad, arm.stl]
2019-10-11 Start work on 3d-printed parts for shooter
    [barrel_parts.FCStd, end_cap.stl, mount.FCStd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]
2019-10-13 Start work on pressure code
2019-10-13 work on sensor classes
2019-10-13 work on ganglion for shooter, and instrument shim
    [barrel_parts.FCStd, end_cap.stl, ganglion.sch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]
2019-10-17 Add mount for pinoon
    [base.FCStd]
2019-10-17 Make grabber arms more robust and design mount for grabber
    [arm.FCStd, grab_mount.stl, grab_servo.stl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]
2019-10-17 Fettle design of barrel parts etc
    [barrel_parts.FCStd, mount.FCStd, ring.stl]
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2019-10-17 add calibration data
    [shooter_cal.csv]
2019-10-17 start work on rotation and bug fix for servo
    [drivetrain.py, servo.py]
2019-10-18 Disable eeprom rubbish and current protection which is borken
2019-10-18 Add rate limiting to pid ? worthwhile??
2019-10-18 Add secondary mount for stability and ?headset (but it doesn't fit...)
    [mount.FCStd]
2019-10-18 Work on laser holder
    [base.FCStd, laser holder.FCStd, laser_holder.stl]
2019-10-18 Bug fix on servo mount for grabber
    [grab_mount.stl, mount.FCStd]
2019-10-20 Start work on servo calibration
2019-10-20 Update shooter and servo, starting work on calibration for shooter...
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2019-10-20 rename drivetrain to Drive and MPU9250 to Orientation
2019-10-20 Turn off servo when program exits
2019-10-20 Start on asyncio framework
2019-10-23 Add hole to attach helmet, hole for data from laser
    [base.FCStd]
2019-10-23 Slightly enlarge main hole in connector shim
    [base.FCStd]
2019-10-26 Work on mount
    [mount.FCStd]
2019-11-02 Redesign of mount
    [mount.FCStd]
2019-11-02 Make space for terminal block
    [laser holder.FCStd, laser_holder.stl]
2019-11-04 Fix modes.Manual: insert sleep in routine
2019-11-04 Enable asyncio debugging Fix unhandled exception error Add fine control with d-pad
    [run_mode.py]
2019-11-04 Change to using microseconds for servo
2019-11-05 Base fettling
    [base.FCStd]
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2019-11-11 Update drivetrain to use new firmware
2019-11-11 Add logging and various bug fixes.
    Navigation with laser and gyro now working
    [drivetrain.py, util.py]
2019-11-11 Refactor to make speed changes happen all at once, rather than per wheel
2019-11-12 add suspension lugs
    [suspension_lug.FCStd, suspension_lug.stl]
2019-11-12 Add read only power registers
2019-11-12 Bug fix in pid.c
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2019-11-12 Fix for wheels.c wheels.h
    [wheels.c]
2019-11-13 Update drivetrain to fit with changes to firmware
2019-11-13 Upgrade drivetrain.py to wokr with new new firmware
2019-11-14 Add error checking on position and power readings
    [drivetrain.py]
2019-11-14 Automatically reset alerts with new commands
    [comms.c, main.c]
2019-11-26 Add debounce delay for button press
2019-11-26 Move event generation into encoder.py
2019-11-26 Tidy up error handling and process control
    [main.py]
2019-11-29 Add Camera to hardware
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2019-11-29 rename ccamera -> camera
2019-11-30 Improve camera calibration routines
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2019-11-30 Make stuff run without headset attached
2020-01-04 Switch to time based speed calculations
2020-01-05 Fix bug in manual drive mode
    [drivetrain.py]
2020-01-06 Various fettlings to make get pid working nicerer
2020-01-06 Add Barrel Stl file
    [Barrel1.stl]
2020-01-14 Add clips for suspension
    [base.FCStd, clip_a.stl, clip_b.stl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]
2020-01-14 Add pinout for connector
2020-01-19 Update clips
    [clips.FCStd, clips.stl]
2020-01-19 Start work on camera distance calibration
2020-02-12 Create card holder for shooter challenge
    [Barrel1.stl, card_holder.FCStd, card_holder.stl]
2020-02-12 Fettle shooter barrel to allow sight adjustment
    [barrel_parts.FCStd, mount.FCStd, sight2.stl]
2020-02-12 Move dance routine to drivetrain
2020-02-16 Add spare laser to kit list
2020-02-18 Add calibration to turning code, improves accuracy to within 1 degree
2020-02-22 Various fixes, major refactoring
    [util.py]
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2020-02-25 Fix bugs in simulated drivetrain
    [drivetrain.py]
2020-02-28 Add Stabber hardware
    [fulcrum2.FCStd, prod_mount.stl, prodder2.stl]
2020-02-29 Simplify camera calibration code...
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2020-03-08 multiple code style fixes
    [drivetrain.py, encoder.py, main.py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]
2020-03-08 Multiple style fixes. Inspect code now returns no errors
    [drivetrain.py, encoder.py, main.py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]
2020-03-08 Add new prodder hardware
    [base.FCStd, fulcrum3.FCStd, mount.stl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]
